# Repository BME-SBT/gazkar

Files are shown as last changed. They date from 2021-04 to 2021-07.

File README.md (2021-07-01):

# BME SBT gázkar
A potméter pozíciójának megfelelő kitöltésű PWM jelet generál. A kiadott jel frekvenciája kb. 50Hz, az impulzusok szélessége 1ms és 2ms között változtatható.

## Bekötés
Felirat | Funkció
--------|--------
5V | 5V tápfeszültség
GND | föld
PWM | PWM jel kimenet, 0-5V
PB0 | [későbbi felhasználásra]
PB1 | [későbbi felhasználásra]
PB2 | engedélyezőjel; 0V:tilt, 5V:engedélyezés

## Programozás
Az ISP pineken keresztül programozható, arduinohoz hasonlóan (AVR ISP). A mikrokontroller ATtiny25.

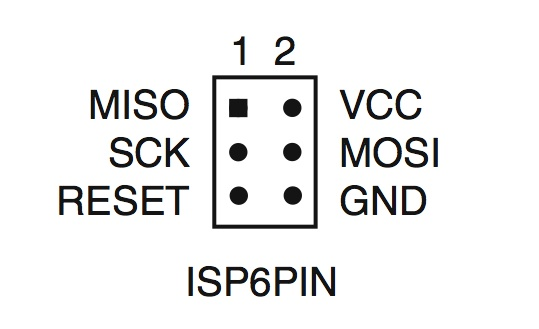
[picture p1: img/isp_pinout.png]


## Debug
DEBUG_SIGNALS macroval fordítva a PB0 és PB1 pineken mérhetők az időzítések

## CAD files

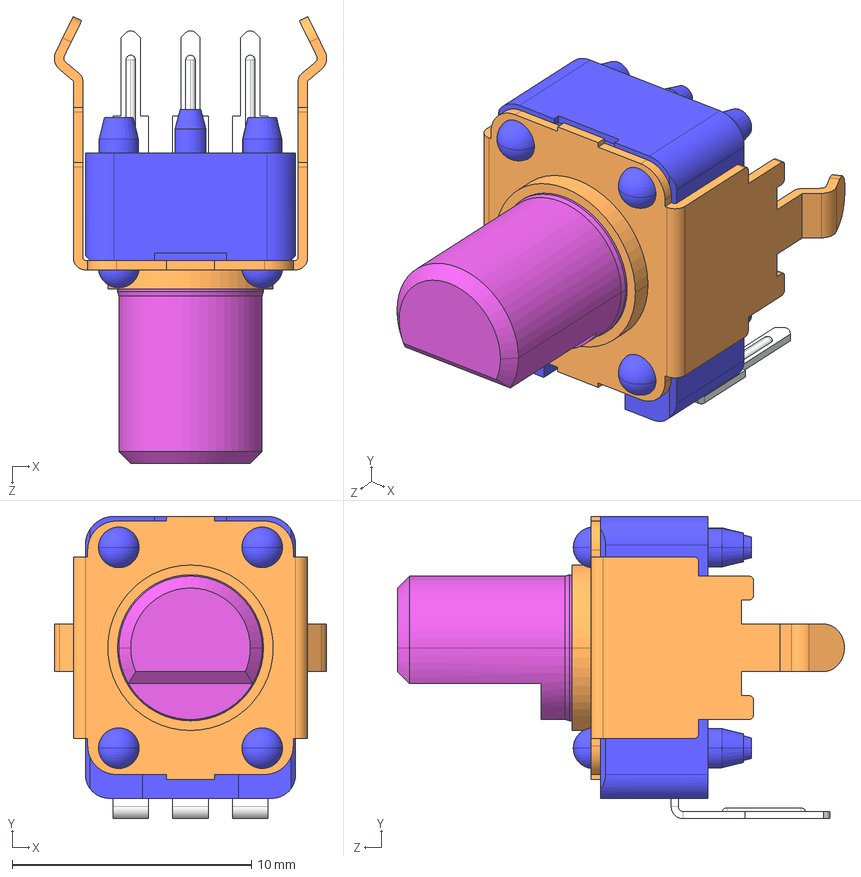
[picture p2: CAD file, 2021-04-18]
hardware/3d/RK09K1130-15.STEP
11.4 x 12.7 x 18.7 mm

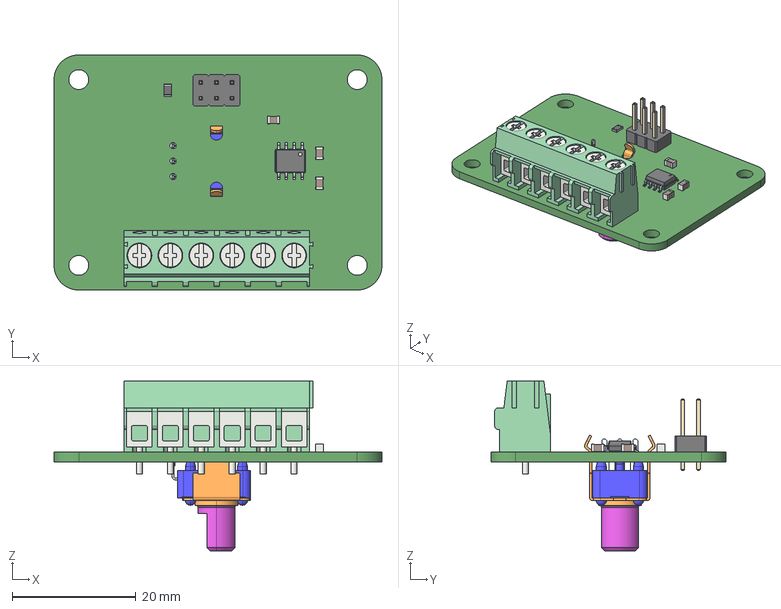
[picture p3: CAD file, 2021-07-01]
hardware/hardware_poti_tuloldal.step
53.0 x 38.0 x 27.4 mm

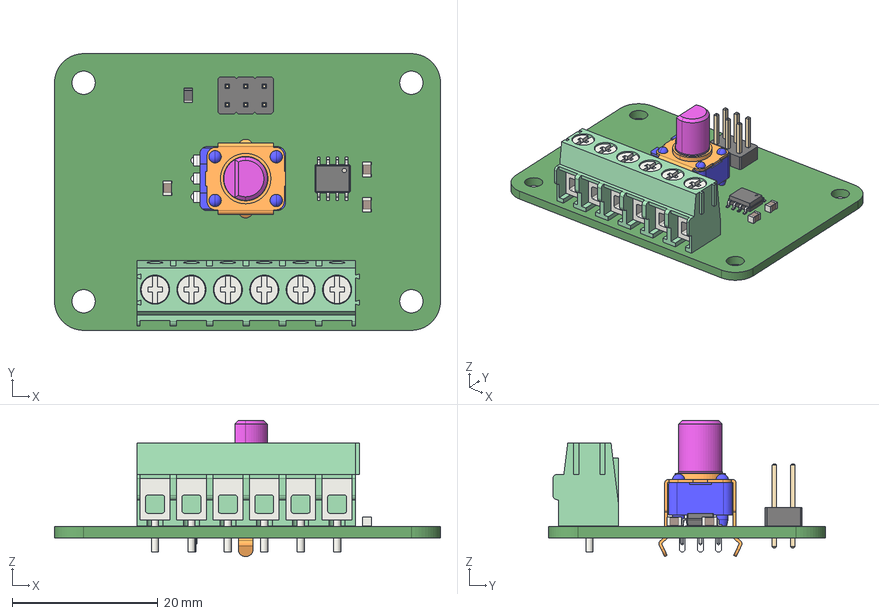
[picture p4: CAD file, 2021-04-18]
hardware/hardware.step
53.0 x 38.0 x 18.7 mm

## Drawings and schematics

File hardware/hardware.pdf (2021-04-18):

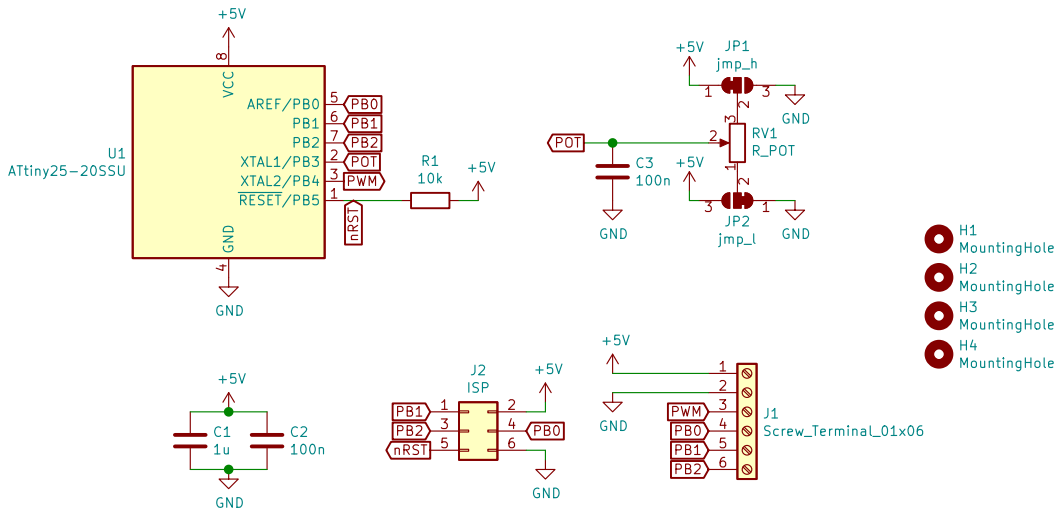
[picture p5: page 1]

Id: 1/1 Title: ATtiny25 PWM controller File: hardware.sch Sheet: / BME SBT

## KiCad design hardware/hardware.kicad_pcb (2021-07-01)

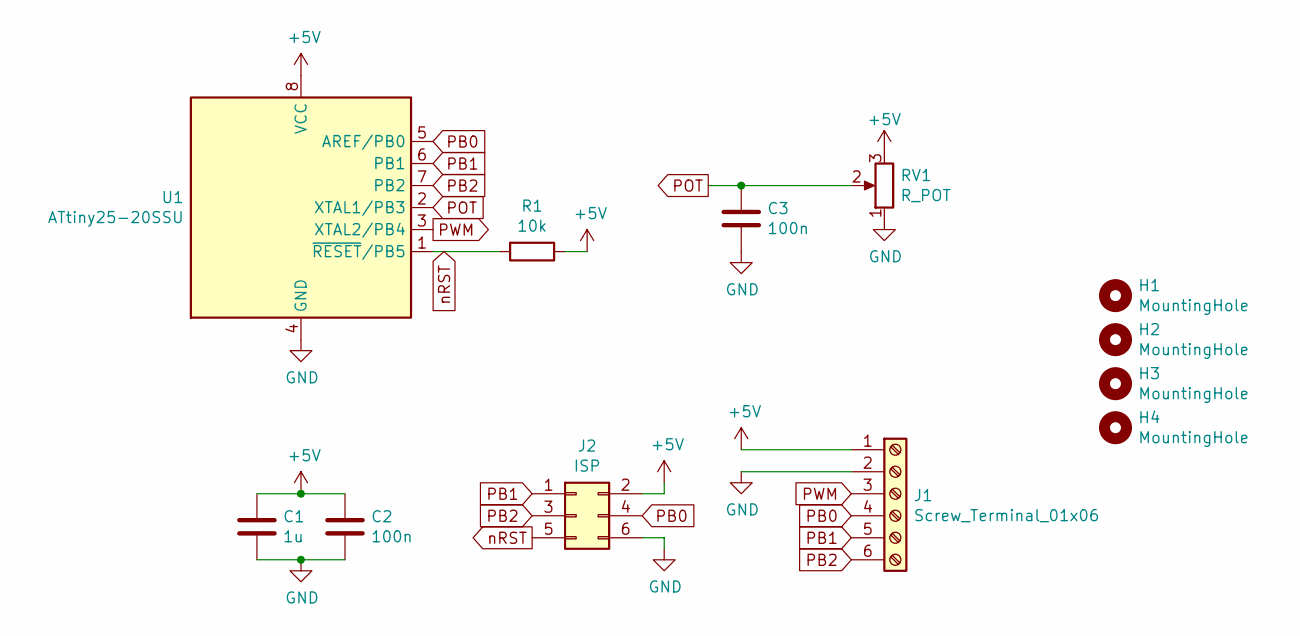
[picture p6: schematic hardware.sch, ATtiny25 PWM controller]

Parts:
C1: 1u; C_0805_2012Metric_Pad1.18x1.45mm_HandSolder
C2, C3: 100n; C_0805_2012Metric_Pad1.18x1.45mm_HandSolder
H1, H2, H3, H4: MountingHole; MountingHole_3.2mm_M3
J1: Screw_Terminal_01x06; TerminalBlock_Phoenix_PT-1,5-6-5.0-H_1x06_P5.00mm_Horizontal
J2: ISP; PinHeader_2x03_P2.54mm_Vertical
R1: 10k; R_0805_2012Metric_Pad1.20x1.40mm_HandSolder
RV1: R_POT; Potentiometer_Alps_RK09K_Single_Vertical
U1: ATtiny25-20SSU; SOIC-8_3.9x4.9mm_P1.27mm

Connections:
+5V: C1.1, C2.1, J1.1, J2.2, R1.1, RV1.3, U1.8 (VCC)
GND: C1.2, C2.2, C3.2, J1.2, J2.6, RV1.1, U1.4 (GND)
PB0: J1.4, J2.4, U1.5 (AREF/PB0)
PB1: J1.5, J2.1, U1.6 (PB1)
PB2: J1.6, J2.3, U1.7 (PB2)
POT: C3.1, RV1.2, U1.2 (XTAL1/PB3)
PWM: J1.3, U1.3 (XTAL2/PB4)
nRST: J2.5, R1.2, U1.1 (~RESET~/PB5)

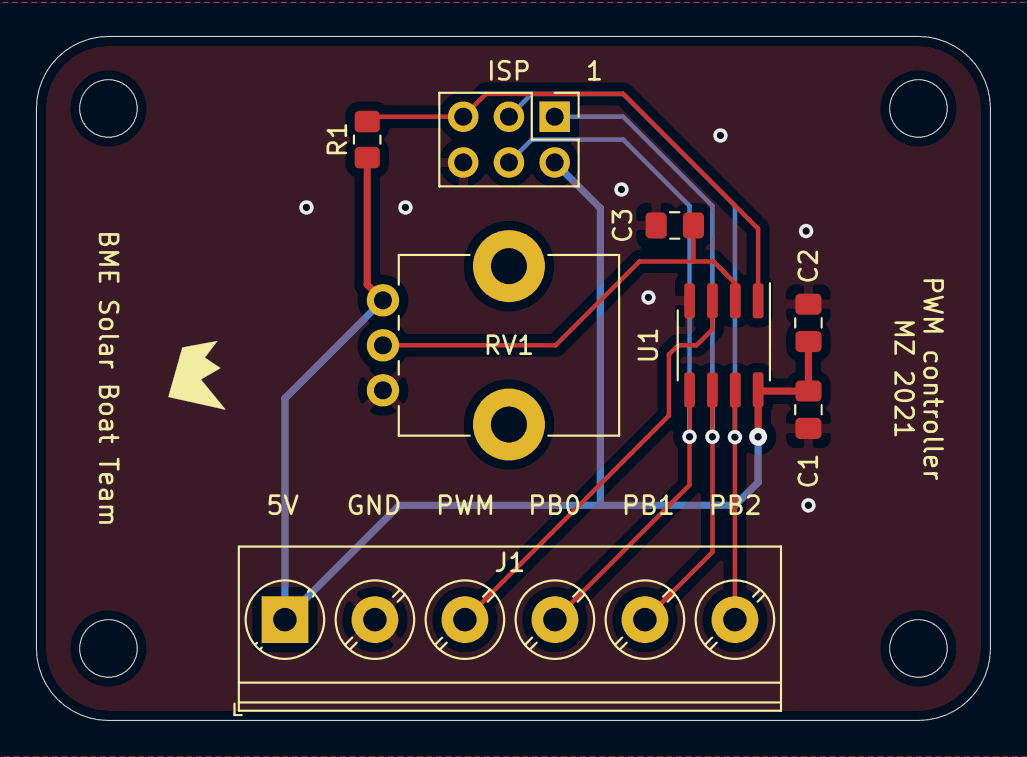
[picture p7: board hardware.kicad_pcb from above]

Board: 2 copper layers, 53.0 x 38.0 mm, 12 parts (0 on the bottom side), 8 nets.

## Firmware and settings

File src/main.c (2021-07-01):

/* Created by Zoltan Marcsek 08.04.2021 */
/*
 * PB3 - Potentiometer input
 * PB4 - PWM output
 * PB2 - Enable input
 */

#define ENABLE_ACTIVE_LOW 0 // Set to 0 for active high, 1 for active low
#define POT_MINIMUM 0       // Scale: 0..255
#define POT_MAXIMUM 255     // Scale: 0..255

/*
 * CLK frequency: 8MHz
 * 
 * Timer0:  interrupt every 20ms, start Timer1
 *          div=1024;clk=7.8125kHz;Cycles=156
 * 
 * Timer1:  single shot, 1-2ms impulse
 *          div=64;clk=125kHz;Cycles=125..250
 * 
 * ADC:     f_s=~4.6kHz
 *          exp. avg. filter:
 *              f_0=615Hz
 *              alpha = 0.875 (7/8)
 */

#include <avr/interrupt.h>

/*
 * If enabled:
 * PB0 will change state when a new PWM period starts
 * PB1 will change state when a new ADC sample is taken
 */
//#define DEBUG_SIGNALS

#define TC1_PRESCALER 0b0111 // Divide by 64
volatile uint8_t tim1_cmp = 255;

int main()
{
    DDRB = (1 << 4);
#ifdef DEBUG_SIGNALS
    DDRB |= (1 << 0) | (1 << 1);
#endif
    // ADC setup:
    ADMUX = 0b0011 | (1 << ADLAR); // input: PB3, left adjust, ref:VCC
    ADCSRA = (1 << ADIE) | 0b111;  // clk=62.5kHz, complete IT
    DIDR0 = (1 << 3);              // disable PB3 DIN
    ADCSRA |= (1 << ADEN);         // enable

    // Timer0 setup:
    TCCR0A = 0b10;          // CTC mode
    TCCR0B = 0b101;         // prescaler=1024
    OCR0A = 155;            // Reset at 155
    TIMSK |= (1 << OCIE0A); // Enable cmpA IT

    // Timer1 setup:
    OCR1A = tim1_cmp;
    TIMSK |= (1 << OCIE1A); // enable cmpA IT
    PLLCSR = 0;

    ADCSRA |= (1 << ADSC); // trigger ADC
    sei();

    while (1)
    {
    }
}

ISR(TIMER0_COMPA_vect)
{
    cli();
    TCCR1 |= TC1_PRESCALER; // start Timer1
    uint8_t in = ((PINB >> 2) & 0x01) ^ ENABLE_ACTIVE_LOW;
    PORTB |= (in << 4); // output ON
#ifdef DEBUG_SIGNALS
    PORTB ^= (1 << 0);
#endif
    sei();
}

ISR(TIMER1_COMPA_vect)
{
    cli();
    TCCR1 &= 0xF0;      // stop timer1
    TCNT1 = 0;          // clear
    PORTB &= ~(1 << 4); // output OFF
    OCR1A = tim1_cmp;   // set compare value
    sei();
}

ISR(ADC_vect)
{
    cli();
    uint8_t adc_scaled = ((uint16_t)(ADCH - POT_MINIMUM) * 255) / (POT_MAXIMUM - POT_MINIMUM);
    uint8_t new = (adc_scaled >> 1) | (1 << 7); // adc value -> 128..255
    uint16_t temp = (7 * new + tim1_cmp) >> 3;  // filter f_0=615Hz
    tim1_cmp = temp;
    ADCSRA |= (1 << ADSC); // trigger ADC
#ifdef DEBUG_SIGNALS
    PORTB ^= (1 << 1);
#endif
    sei();
}

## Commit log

2021-04-18 Add hardware
    [RK09K1130-15.STEP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]
2021-07-01 things changed
    [hardware-B_Cu.gbr, hardware-B_Mask.gbr, hardware-B_Paste.gbr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]
